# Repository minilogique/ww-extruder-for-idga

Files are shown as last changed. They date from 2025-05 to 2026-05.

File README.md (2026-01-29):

WristWatch extruder with OEM IDGA gearset.

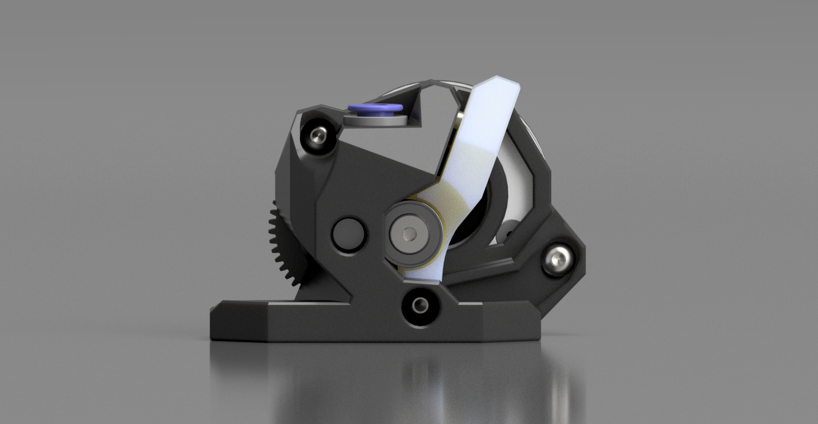
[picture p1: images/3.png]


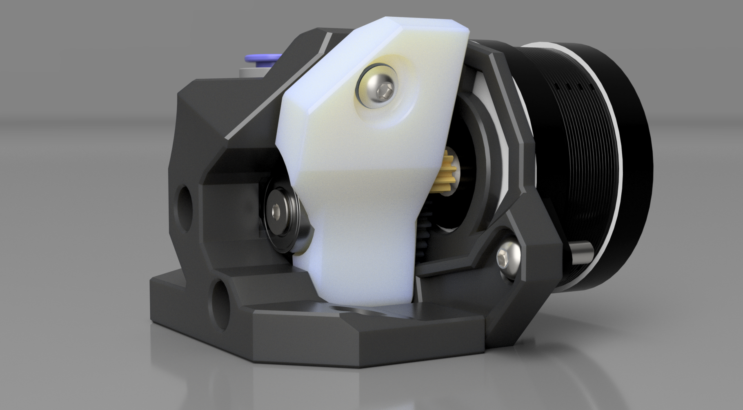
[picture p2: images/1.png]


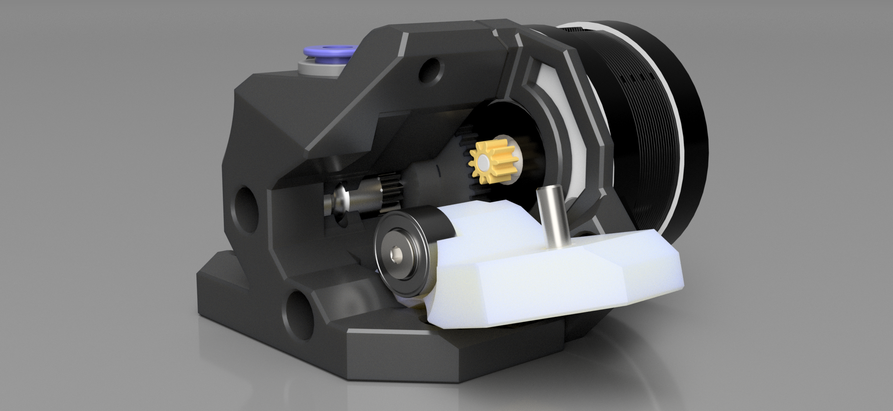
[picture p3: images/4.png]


To see it in action pushing 95A TPU at 29mm3/s https://www.youtube.com/watch?v=95B_EeGK_1Y

Had an OEM IDGA gearset laying around and I had nothing else to do with it. Clockwork2 seemed to be unecessarily complex so I opted to butcher WristWatch2 BMG version to make it fit IDGA as it's already fairly similar. Needed to move the filament path 9.25mm forward and match the mounting pattern, because of that the extruder is a bit longer and stepper is farther away for that amount.

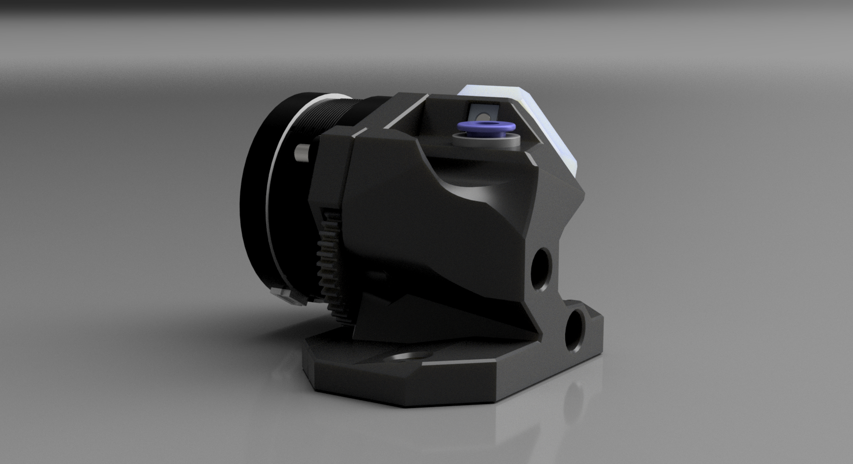
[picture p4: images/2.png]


## BOM
```
Main hardware
2 M3 thin square nuts
2 M3x20 (1 M3x20 if you do not use smooth idler)
1 M3x12 (2 M3x20 if you do not use smooth idler)
1 M3x16
1 M3x25
1 OEM IDGA gearset
1 M3 thin washer
1 extruder spring

For smooth idler
1 685-2RS bearing
1 flathead M3x16
1 M3 thin washer

```

Used hardware is identical to WW extruder list except the gearset. Print settings are recommended to be of official Voron spec. Centre of Mass is shifted so it quite possibly will affect your resonance with more aggressive print settings. Parts except idler arm are printed as oriented in the files. Drilling/cleaning filament path with 2mm nail/drillbit might be needed depending of your print quality.

- Update 21.12.2025 - increased radius for smooth idler arm around the bearing and added a sleeve that fits the bearing to reduce the play and possible binding when arm bends under load.
- Update 11.03.2025 - uploaded new models, improved looks and strength, added integrated supports for tension arm model. Improved the visuals for smooth idler bearing arm. Created Github page, added BOM.
- Update 21.05.2025 - fixed 3mf files, modified descriptions.
- Update 29.11.2025 - reduced main drive axle tolerances to 0.333mm or about 0.16mm around the axle to further improve TPU reliablity. Re-did the renders aswell and updated the CAD file.
- Update 29.01.2026 - aesthetical changes for "MAIN BODY", updated CAD, new renders.

Also available at https://www.printables.com/model/1154980-wwbmg-wristwatch-extruder-for-idga-not-ridga-with

I went a bit further with the idea for more torque, cheaper to build WW MK8 at https://github.com/minilogique/WristWatch-MK8

Original source for the mod idea came from https://github.com/Armchair-Heavy-Industries/A4T

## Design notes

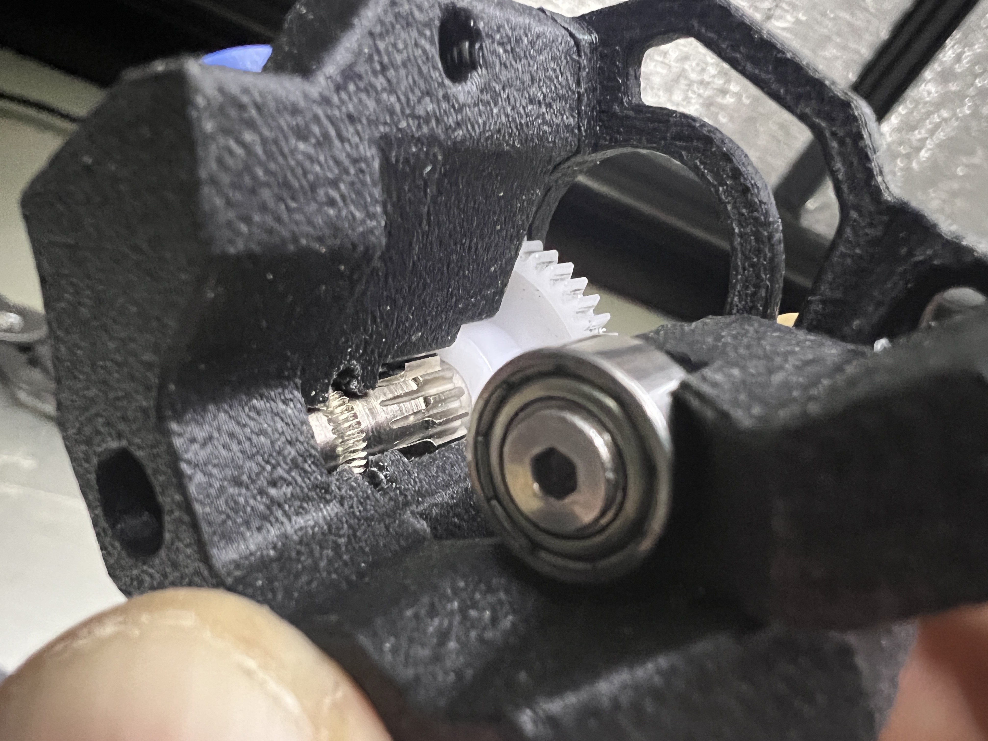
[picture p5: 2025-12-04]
images/core.JPG

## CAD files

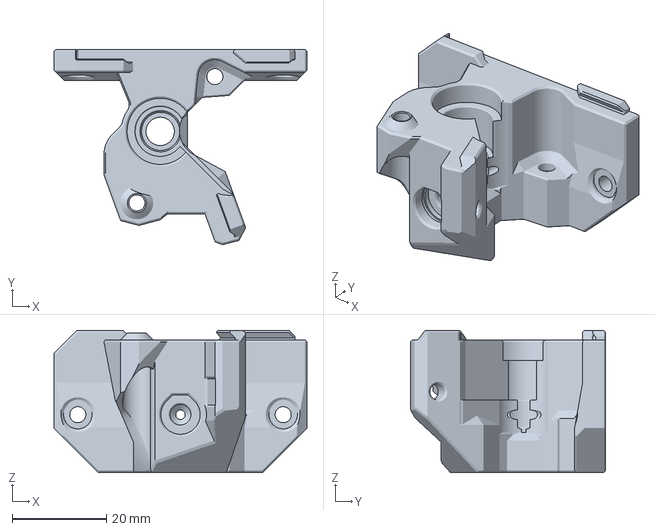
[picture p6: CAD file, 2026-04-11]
STLs/WWBMG IDGA MAIN BODY.3mf
53.6 x 41.4 x 30.1 mm

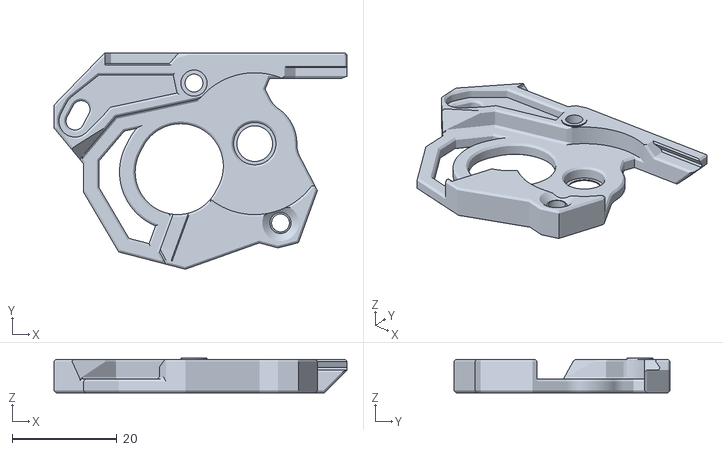
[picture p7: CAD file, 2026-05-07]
STLs/WWBMG MOTOR PLATE.stl
56.0 x 41.4 x 6.60

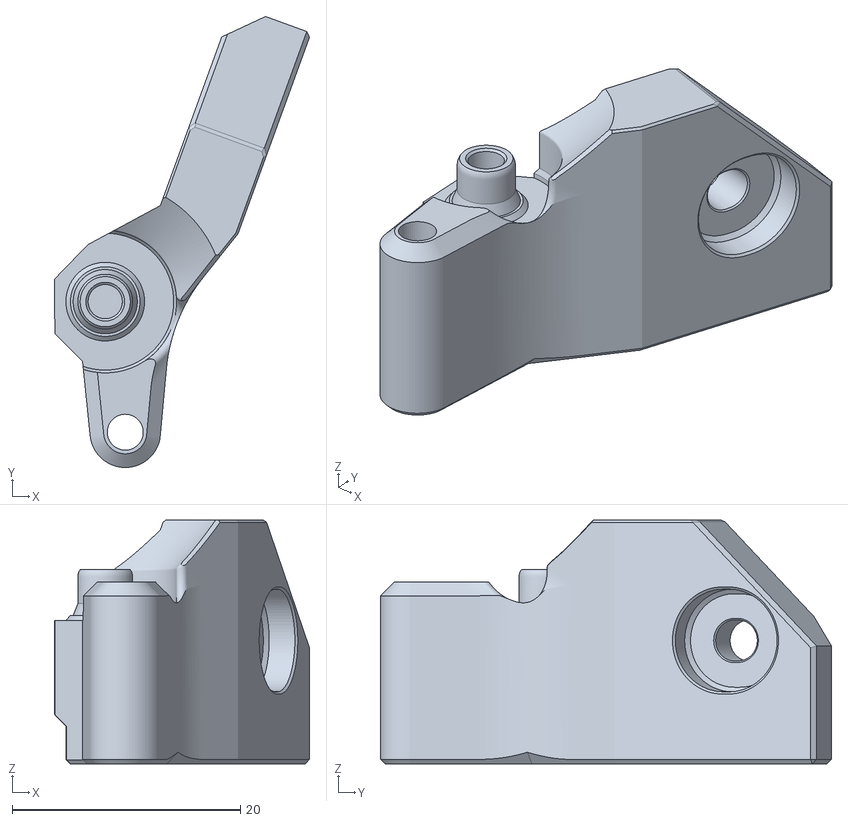
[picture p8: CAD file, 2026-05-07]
STLs/WWBMG SMOOTH IDLER TENSION ARM.stl
22.4 x 39.6 x 21.4

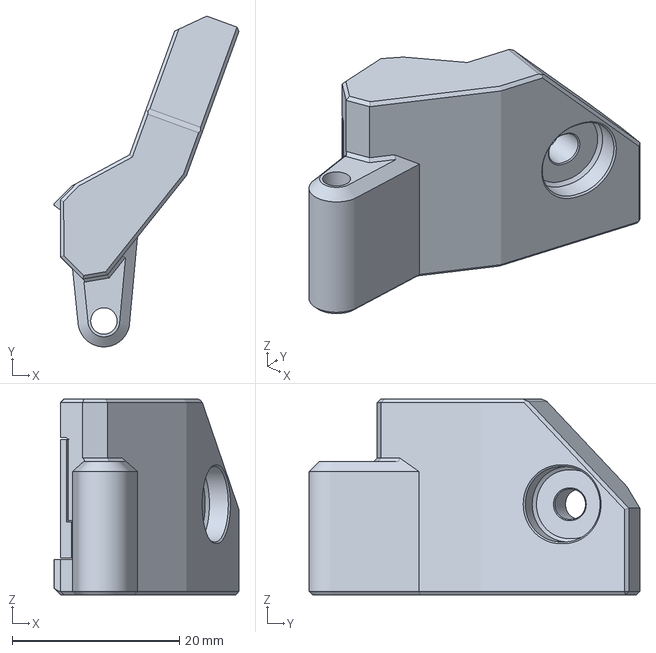
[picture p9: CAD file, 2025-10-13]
STLs/WWBMG GEARED IDLER TENSION ARM.3mf
22.1 x 39.6 x 23.4 mm

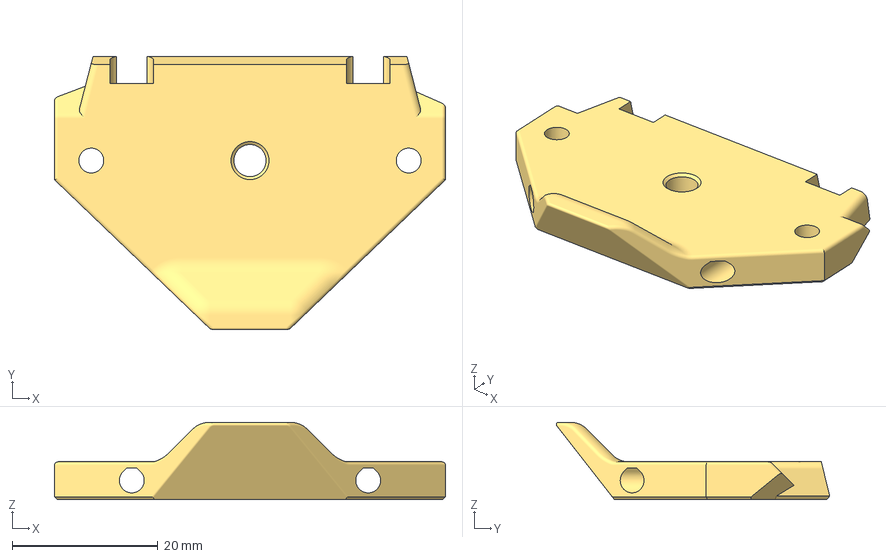
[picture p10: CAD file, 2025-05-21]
STLs/A4T - WWBMG - Extruder Adapter [cw2-tap].3mf
53.6 x 37.5 x 10.6 mm

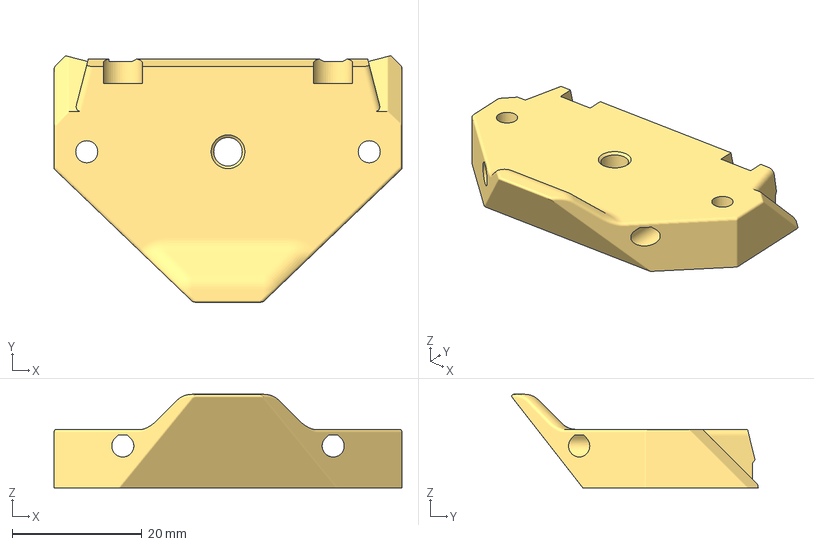
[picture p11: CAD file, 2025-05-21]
STLs/WWBMG EXTRUDER ADAPTER for A4T with 3.8mm raise.3mf
53.6 x 38.0 x 14.4 mm

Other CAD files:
STLs/WWBMG BEEFIER MOTOR PLATE.stl

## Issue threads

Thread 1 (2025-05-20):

3mf files are project save files, not models

HumbleDeer, 2025-05-20:
The 3MF files are formulated as a project savefile from a slicer, not as an exported model file from a CAD program. They're currently incompatible with a few different pieces of software because of that.

minilogique, 2025-05-21:
working on it

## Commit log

2025-03-11 no supports needed
    [WWBMG IDGA MAIN BODY.3mf, WWBMG IDGA MOTOR PLATE.3mf, WWBMG IDGA TENSION ARM SMOOTH IDLER.3mf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]
2025-03-11 trying to figure out how this thing works
    [WWBMG IDGA MAIN BODY.3mf, WWBMG IDGA MOTOR PLATE.3mf, WWBMG IDGA TENSION ARM SMOOTH IDLER.3mf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]
2025-03-11 still figuring out how this works
    [WWBMG IDGA MAIN BODY.3mf, WWBMG IDGA MOTOR PLATE.3mf, WWBMG IDGA TENSION ARM SMOOTH IDLER.3mf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]
2025-03-12 updated files and folders
    [WWBMG IDGA MAIN BODY.3mf, WWBMG IDGA MOTOR PLATE.3mf, WWBMG IDGA TENSION ARM SMOOTH IDLER.3mf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]
2025-03-17 updated the tension arm
    moved the idler center point 0.15mm lower for better alignent due to difference in diameters between IDGA shaft and the bearing
    [WWBMG IDGA TENSION ARM SMOOTH IDLER.3mf]
2025-03-20 fixed ECAS clearance on main body
    [WWBMG for IDGA main body.stl]
2025-05-21 fixed 3mf files
    instead of slicer saves I reuploaded version exported straight from Fusion
    [WWBMG IDGA MAIN BODY.3mf, WWBMG IDGA MOTOR PLATE.3mf, WWBMG IDGA TENSION ARM SMOOTH IDLER.3mf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]
2025-05-21 fixed adapter files
    added A4T extruder adapter that I added 3.8mm of height and also the direct file from A4T git just so all the necessary stuff is available from one place
    [A4T - WWBMG - Extruder Adapter [cw2-tap].step, WWBMG EXTRUDER ADAPTER for A4T with 3.8mm raise.3mf, WWBMG for IDGA A4T EXTRUDER ADAPTER.3mf]
2025-05-21 replaced files with correct file format
    [A4T - WWBMG - Extruder Adapter [cw2-tap].3mf, A4T - WWBMG - Extruder Adapter [cw2-tap].step]
2025-05-21 added tension arm for idler gear
    [WWBMG GEARED IDLER TENSION ARM.3mf]
2025-10-13 Update WWBMG GEARED IDLER TENSION ARM.3mf
    added some extra material to the face side for extra strength and durability
    [WWBMG GEARED IDLER TENSION ARM.3mf]
2025-10-31 file system renaming, added metadata
    [A4T - WWBMG - Extruder Adapter [cw2-tap].3mf, WWBMG EXTRUDER ADAPTER for A4T with 3.8mm raise.3mf, WWBMG GEARED IDLER TENSION ARM.3mf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]
2025-11-29 updates on main body, updated main body and new renders.
    reduced the tolerances for main drive shaft to 0.16mm and slimmed the body down a bit for better adjustability by hand from the left side of the extruder via main hob.
    [WWBMG IDGA MAIN BODY.3mf]
2025-12-15 Update WWBMG SMOOTH IDLER TENSION ARM.3mf
    added bearing clearance radius; beefed up the bearing mounting bump; reduced bolt hole diameter;
    [WWBMG SMOOTH IDLER TENSION ARM.3mf]
2025-12-21 idler update, CAD update
    [WWBMG SMOOTH IDLER TENSION ARM.3mf]
2026-01-28 aesthetic changes
    [WWBMG IDGA MAIN BODY.3mf]
2026-02-27 updated clearances of the main body to better suit with softer TPU materials with smooth idler; tweaked the smooth idler tension arm for clearances
    [WWBMG IDGA MAIN BODY.3mf, WWBMG SMOOTH IDLER TENSION ARM.3mf]
2026-04-11 minor clearance fixes
    [WWBMG BEEFIER MOTOR PLATE.3mf, WWBMG IDGA MAIN BODY.3mf, WWBMG SMOOTH IDLER TENSION ARM.3mf]
2026-04-11 bearing position adjustments
    [WWBMG IDGA MAIN BODY.3mf]
2026-05-07 replaced some 3MFs with STLs due to somehow still having printer profiles attached to them
    [WWBMG BEEFIER MOTOR PLATE.3mf, WWBMG BEEFIER MOTOR PLATE.stl, WWBMG MOTOR PLATE.3mf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]
